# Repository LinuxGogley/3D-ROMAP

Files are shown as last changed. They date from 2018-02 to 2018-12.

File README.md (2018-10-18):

# CECS 490 - Senior Design Project
3D Robotic Mapping Platform (3D ROMAP) - designed at California State University Long Beach.

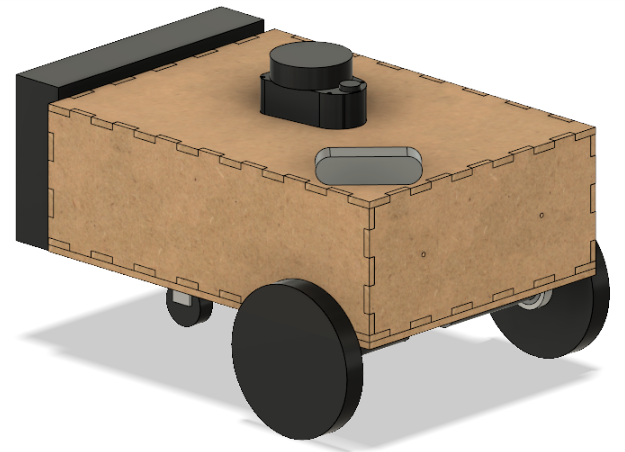
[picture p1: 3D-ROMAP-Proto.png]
Prototype Assembly


## Sponsored by Advanced Circuits
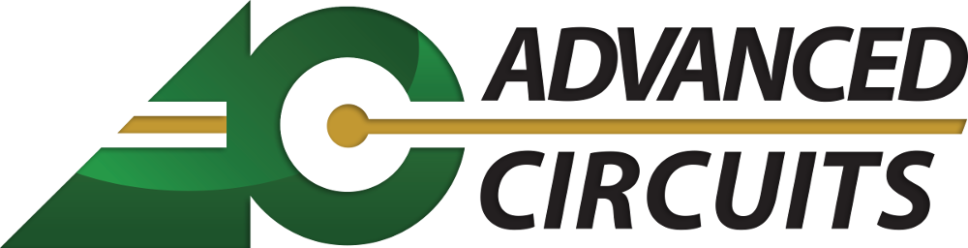
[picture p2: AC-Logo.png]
Sponsored By Advanced Circuits


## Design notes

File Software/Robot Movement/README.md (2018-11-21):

# Source code for Bluetooth Controlled Robotic Movement
* Uses bluetooth for wireless control of motors (WASD controls) 
* Uses two motors with seperate speed and direction controls
* Hardware: 
1. HC05 Bluetooth Module
2. MC33926 H-Bridge
3. TM4C Microcontroller
4. 2x DF Robot Motor 12V, 3.6A, 146RPM

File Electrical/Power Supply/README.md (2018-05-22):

# Power Supply
Schematic in PDF format, with directories containing source files and documentation pertaining to the power supply.

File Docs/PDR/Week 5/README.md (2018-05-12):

# PDR - 2018 April 22
PDR documents IMU, change from MS Kinect to Realsense, updated block diagram, and power
reqs updated.

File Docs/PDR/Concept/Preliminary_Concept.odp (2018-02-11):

## Preliminary Concept

TeaM4C (R Dominick, L Gogley, M Munoz, D Tran)

## Requirements

- The design shall map unknown coordinates through exploration.
  - Location of choice should not dictate mapping method, i.e. a room vs a field.
- The design shall not be limited to enclosed or man-made structures.
  - The scans must be accurate enough to recognize a low profile object as an obstacle/structure in its map.
- The design shall be capable of 2D SLAM.
  - SLAM shall be used to handle 2D mapping.
- The design shall be capable of 3D capture.
  - 3D capture can be pulled from samples or from real-time/soft real-time capture.
- The design shall be powered from an independent power supply.
  - This power source shall provide enough power to explore, at minimum, one floor of the ECS building.

## Limitations

- The design is not confined to color recognition of the surroundings.
  - With use of LiDAR, the capture is not interested in color, therefore detail is lost of surroundings.
- The design is not confined to autonomous navigation, simply the capability of such.
  - The design will be capable of mapping and localization, but the platform may not drive autonomously as functionality of mapping is the first priority.
- The design is not confined to real-time 3D mapping, due to limitations of price and available algorithms.
  - Real-time 3D is sometimes limited to ability of hardware readout, and may be an unrealistic endeavor. 3D may instead be done from sampling.
- The design is not interested in object recognition.
  - Point clouds will be used to simply display raw data, and points on a 2D plane will only be used to determine the explored area.

## Purpose of Design

- For us:
- Explore high performance embedded system design.
- Expand territory into industry applications such as point cloud capture, machine vision, and SLAM.

## Purpose of Design

- For the consumer:
- 3D maps introduce depth to a panoramic capture, and allow for implementations such as virtual real estate, virtual visits to landmarks, and cave, ocean, or other exploration.
- This platform will serve as a self-contained system capable of remembering where it began its journey, while also creating a map of the area it explores beyond that point.

## Top Level Block Diagram

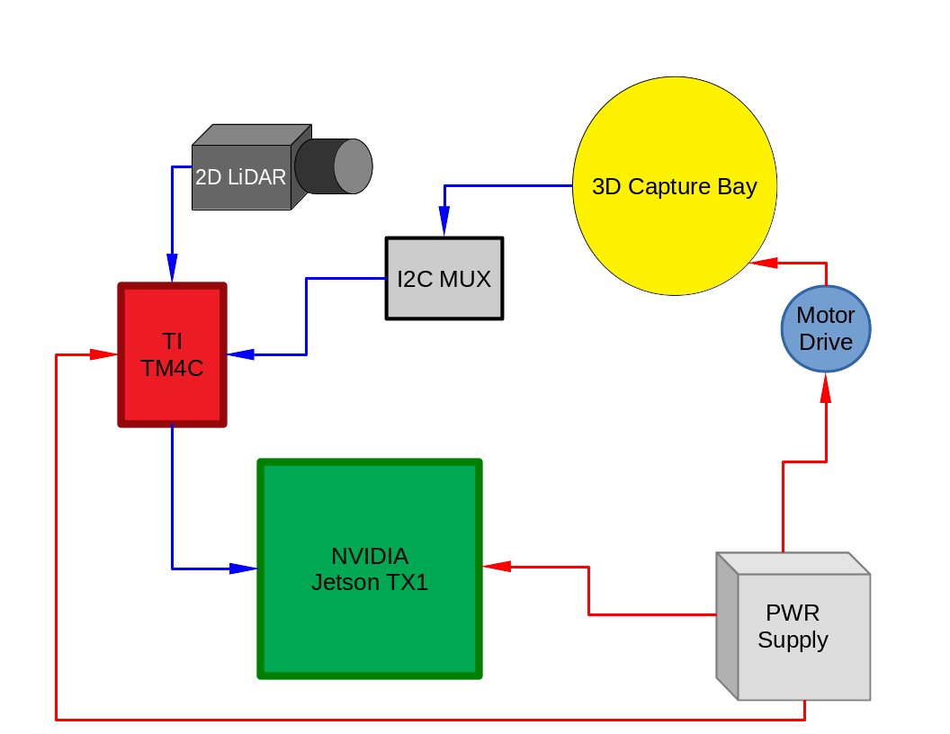
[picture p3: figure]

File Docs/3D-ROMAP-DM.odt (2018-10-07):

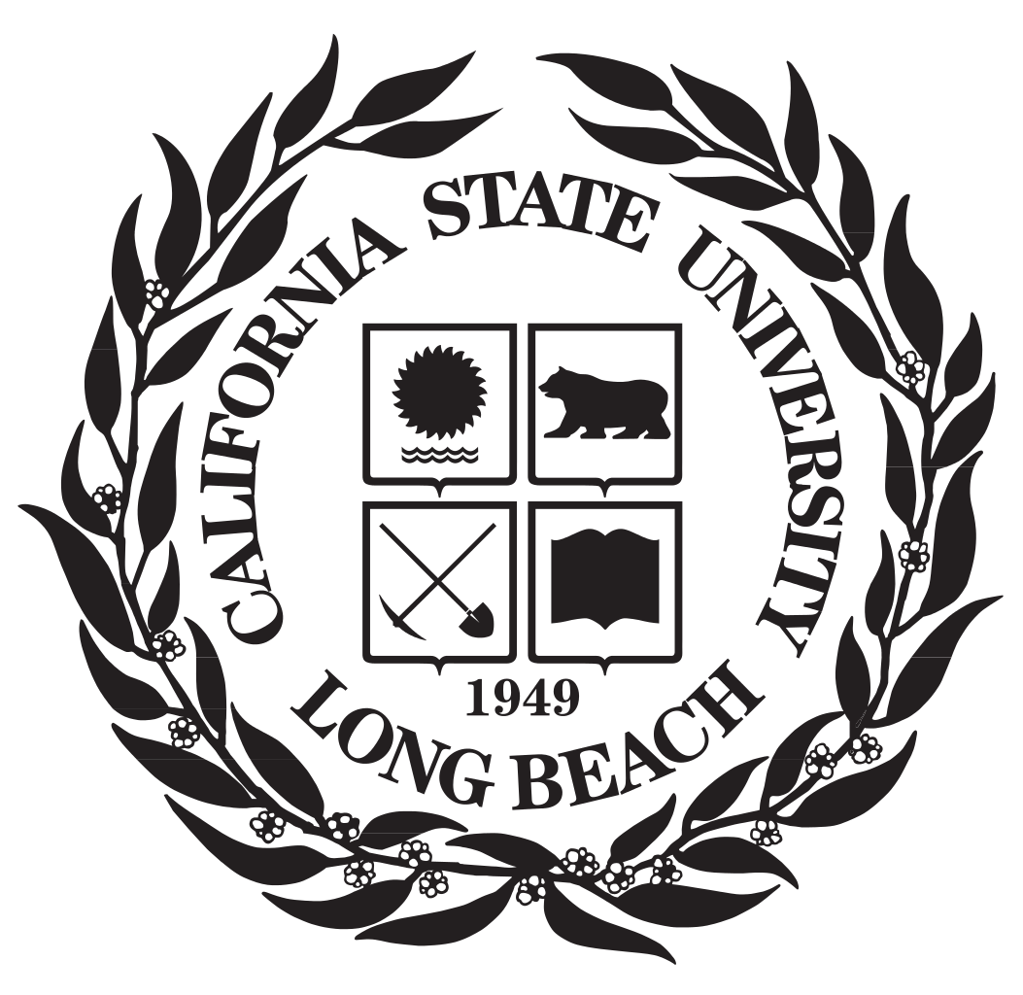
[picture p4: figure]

3D-ROMAP

Design & Methodology Document

CECS 490

Revision: C

California State University, Long Beach

The contents of this document may not be reproduced in whole or in part without the written

consent of the owner.

NOTICE

ALL STATEMENTS, INFORMATION, AND RECOMMENDATIONS IN THIS MANUAL ARE BELIEVED TO BE ACCURATE BUT ARE

PRESENTED WITHOUT WARRANTY OF ANY KIND. NOT WITHSTANDING ANY OTHER WARRANTY HEREIN, ALL DOCUMENT FILES

AND SOFTWARE ARE PROVIDED “AS IS” WITH ALL FAULTS. I DISCLAIM ALL WARRANTIES, EXPRESSED OR IMPLIED,

INCLUDING, WITHOUT LIMITATION, THOSE OF MERCHANTABILITY, FITNESS FOR A PARTICULAR PURPOSE AND

NON INFRINGEMENT OR ARISING FROM A COURSE OF DEALING, USAGE, OR TRADE PRACTICE.

IN NO EVENT SHALL I BE LIABLE FOR ANY INDIRECT, SPECIAL, CONSEQUENTIAL, OR INCIDENTAL DAMAGES, INCLUDING,

WITHOUT LIMITATION, LOST PROFITS OR LOSS OR DAMAGE TO DATA ARISING OUT OF THE USE OR INABILITY TO USE THIS

MANUAL, EVEN IF I HAVE BEEN ADVISED OF THE POSSIBILITY OF SUCH DAMAGES.

Rev History

Revision Number | Release Date | Description
A | 2018-03-22 | Initial release
B | 2018-05-22 | Preliminary data added
C

Index of Tables

Table of Figures

Preliminary Chassis Concept 16

Top Level Block Diagram 17

MCU detailed block diagram 18

Processing board detailed block diagram 23

Voltage rails and current 26

Power requirement and power draw per channel 26

Alkaline battery discharge 27

Deep cycle sealed lead acid discharge 28

LiFePO4 runtime discharge 28

LiFePO4 capacity discharge 29

18V and 12V DC-DC Converter 30

5V LDO to MCU and LiDAR 30

SLAM Software Flow 31

# Acronyms and Abbreviations

Abbreviation | Description | Abbreviation | Description
°C | Celsius | PCL | Point Cloud Library
°F | Fahrenheit | PWM | Pulse Width Modulation
A | Amps | Rev | Revision
COMM | Communication | SLAM | Simultaneous Localization and Mapping
CPU | Central Processing Unit | TBD | To Be Determined
dB | Decibels | UART | Universal Asynchronous Receiver Transmitter
ESD | Electrostatic Discharge | USB | Universal Serial Bus
FAT | File Allocation Table
FOV | Field of View
ft | Feet
g | Gram
GPU | Graphics Processing Unit
GUI | Graphical User Interface
mA | Milliamps
I²C | Inter-Integrated Circuit
I/O | Input/Output
ICD | Interface Control Document
ID | Identification
IR | Infrared
km | Kilometer
LDO | Low Dropout
LSB | Least Significant Bit
mm | Millimeter
ms | Millisecond
MSB | Most Significant Bit
NIR | Near Infrared
OEM | Original Equipment Manufacturer
PCD | Point Cloud Data

# Reference Documentation

The following documents form part of this specification. In the event of a conflict between

documents referenced herein and the contents of this specification, the contents of this specification

shall be considered a superseding requirement.

Document No:

# Scope

This document describes the design characteristics for the 3D-Robotic Mapping Platform (3D -ROMAP).

# Project Overview

The following research project documented in this report details a three-dimensional room mapping robot. The robot will be able to enter various rooms and be remotely controlled by the user. While the robot is in the specified environment, it will map the surrounding area in both a two-dimensional and three-dimensional representation. The user will then be able to view the generated maps on a separate remote desktop for observation purposes. The robot will combines various sensors in order to scan the environment around it and will utilize that data to determine its location in the current environment that it is exploring. This research project explores advanced image capturing techniques, navigation of unknown environments, as well as practical applications of electrical and mechanical engineering practices.

# Project Description

The implementation of our project involves the utilization of an onboard GPU-accelerated embedded computer that will process the data received from both the LiDAR sensor and the Intel Realsense IR Depth Camera. A cost-efficient microcontroller will also be utilized to interface with not only the LiDAR sensor but also the various motors including DC motors and a single stepper motor.

The LiDAR sensor will be mounted on platform that will be rotating at a fixed frequency through the use of a stepper motor. The LiDAR will return a distance value which will be utilized to generate a 2D representation of the environment. In order to accomplish this, the TM4C will send the both the distance value as well as the angle that the stepper motor is at to the Jetson board for processing. The Jetson will then generate a two-dimensional cartesian coordinate plane with those sampled points plotted on it, which will become the two-dimensional representation of the overall environment around the robot. The sensor along with the rotating platform will be mounted at the top of the robot’s chassis.

The Intel Realsense camera will be mounted at the front of the robot and will be utilized to extract depth and image data of the surrounding environment in front of it. The robot will capture the data at a fixed rate. This data will be output as a .pcd file format The data must then be filtered in order to reduce the distortion that occurs in the RGB point cloud capture for the user’s observability. After the data has been captured as a point cloud, the data will then be stitched with other point cloud captures in post-processing. Due to uncertainty with the data compilation not being able to keep up with real time capture rates, we will not be performing the stitching in real-time. Instead we will stitch the point clouds generated using an open source utility software called Cloud Compare.

The position of the robot in the given environment will be determined through the utilization of SLAM, or simultaneous localization and mapping. The details of the algorithm itself will be elaborated in a further section of this documentation.

These technologies will be powered from a custom-built power supply designed by us. We chose the NVIDIA Jetson TX1 to perform the main computations and instruction executions for various reasons including: its powerful processing capabilities, 256 CUDA core GPU, and the ability to load a flavor of Linux to debug and control the software running. Most of our focus will be distributed towards capturing and processing the data from the sensors, and point cloud generation of our given position in the environment. The 3D representation will be sent using a mounted commercial off the shelf (COTS) router to generate a local WiFi connection for remote desktop connection. A static IP will be assigned to the Jetson, and the remote protocols of interest are VNC, SSH, X2Go, and RDP.

# Similar Projects

MIT NVIDIA Jetson RACECAR:

Students at MIT developed a “Rapid Autonomous Complex-Environment Competing Ackermann-steering Robot”, or RACECAR using the NVIDIA Jetson TX1 to process the data from their sensory suite. The goal was to design and implement various SLAM algorithms that would allow the vehicle to navigate a tunnel fully autonomously without human intervention. Our project will also utilize the NVIDIA Jetson TX1 to process our sensory data and generate the 2D and 3D maps for the user to observe on a remote desktop. This project shows that the hardware has the power and capability to successfully perform the task.

DARPA SLAM Car:

In 2005, DARPA issued the DARPA Grand Challenge, which was a competition where driverless cars would compete on an off-road course to determine which vehicle could autonomously navigate it the fastest. The winning vehicle, named “Stanley”, successfully navigated the course the fastest with a time of 6 hours and 54 minutes. The vehicle utilized several technologies including: five LiDAR sensors to generate a 3D map of the environment to aid their GPS’s positional sensing capabilities, a video camera to observe driving conditions, and an odometer to calculate how far the vehicle had traveled if the other sensors could not extrapolate enough data to determine its given position. Six low-power computers running Linux operating systems were also used to process the sensor data. Our project will share a few similarities with this design, including the utilization of Linux OS on the NVIDIA Jetson TX1 to process and execute instructions based on the data obtained from our single LIDAR sensor. We will also be utilizing the LIDAR sensor to generate a 2D map rather than a 3D map; instead, we will use an Xbox Kinect to perform the 3D mapping of the environment.

# Project Significance

For our group, this project will serve as an in-depth introduction to vision systems, high performance embedded computing, power management, and exploration of robot localization techniques. This is intended as a research project in which the concepts listed above are implemented into a single functional design. We would hope that with further implementation, this research would result in possible consumer products such as advanced visual street maps and rescue platforms for victims of natural disasters.

# Requirements

In order to create a clear end goal for our design, the following requirements describe the necessary elements to satisfy our project of creating a 3D robotic mapping platform:

The design shall map unknown coordinates through exploration on passable terrain

The initial goal of the design was to be able to map an unknown location. The current build of the project is intended to be demonstrated in an office environment, so the qualification of “passable terrain” has been defined as our exploration environment.

The design shall be capable of 2D SLAM

To keep us directed towards the SLAM based side of the research, we have specified that the research should be capable of 2D SLAM with the implementation of the PulsedLight LiDAR Lite. 3D SLAM has been omitted as a requirement to ease completion.

The design shall be capable of 3D capture

Our design needs to be able to capture an environment in 3D in a point cloud format. Our capture must be real time, however the design does not have to process and stitch images together in real time. This condition has been limited to post processing, as we fear data compilation may not be able to keep up with real time capture rates.

The design shall be capable of producing a visual map from 3D capture

Individual 3D point clouds are required to be stitched together to form a completed 3D representation of the environment. Stitching two images together has prove to be successful manually, however the automation of this process is the end goal.

The design shall be powered from an independent power supply

A custom power supply is being designed for this project. While the battery source has yet to be selected, we are expecting a 24V input battery source. The power supply will efficiently step down the voltage to 18V and 12V using a DC-DC buck converter, and 5V using a 12V source through an LDO. The component of interest is the Texas Instruments TPS54531 for high current applications to the 18V and 12V rails, while the ST LD29150 will provide an efficient low power feed to the 5V rail to the MCU. During operation, the project should be capable of running a minimum of 20 min, which in turn allows for a 20 min room capture.

# Work Breakdown

Due to the complexity of this endeavour, we wanted to make efficient use of our large group by dividing the work into two teams of two. This ensures that both teams have at least one person to collaborate with, and that no members are excluded from meaningful contribution to the project.

The two teams will be assigned one categorical task which will encompass the heart of our design. These categories are: 3D capture and SLAM implementation.

These tasks will be our first priorities for our path to success, as they will create the baseline for our first working prototype. Below lists the two categories, and the requirements for fulfilling the task.

## 3D Capture

Intel Realsense Capture

Task to interface with the Intel Realsense D435 stereo vision camera using the official SDK. From this capture we will extract depth and image data from the surroundings to form matrices. Due to the inaccuracies of stereo vision technology, we will be sampling and filtering the data before generating a point cloud of the capture.

3D Point Cloud

Task to associate the IR distance data to image data in a rendered point cloud using the Realsense SDK, and the Point Cloud Library (PCL) platform to generate the 3 dimensional depth structures.

3D Rendering

Task to use 3D rendering software to generate the visual of our stitched result. This task will be accomplished by capturing the point cloud in a supported 3D format such as the Polygon (PLY) format or Point Cloud Data (PCD) format. The post-processing is accomplished with the Open-Sourced utility Cloud Compare, for the point cloud registration and stitching.

## Simultaneous Localization and Mapping (SLAM)

Algorithm

Task to research algorithms to track robot’s position as it explores a room. Our preliminary algorithm can be seen in flowchart format in the software section. The algorithm flows as follows: gather positional changes from movement sensors like the odometers and accelerometers, and use this data to create an initial estimate of where the robot is in its environment. Next, gather data from environmental sensors, such as the LiDAR distance sensor, relate it to data previously collected from the environmental sensors, and combine them to create a more accurate position estimation.

Hardware Capture

Task to research and prototype methods of capturing distance data of the surroundings to be used by SLAM. This includes distance measurements from our LiDAR sensor, positional change from motor odometers, angular velocity from our gyroscope, directional acceleration from our accelerometer, or changes in magnetism (essentially a compass).

SLAM Implementation

Task to implement the chosen algorithms with hardware to feed positional data to 3D rendering for completion of 3D mapping robot. Our implementation will be based on Google Cartographer, which incorporates range data (LiDAR Lite V1), IMU data (MPU-9250), and odometry data (wheel encoders) to enable our robot to simultaneously localize and map the environment around it in a two-dimensional implementation. We chose to utilize Google Cartographer because it is open source software and fits well with our selected components.

# Design Overview & Operation

Our robot design utilizes a microcontroller and an onboard processing computer to handle the various sub-components of the overall system. The microcontroller will handle motor control and will interface with an HC-05 bluetooth module as well as a LiDAR sensor. The onboard computer; the NVIDIA Jetson TX1, will be utilized to interface with our Intel Realsense IR stereo vision camera and will process and generate the 2D and 3D maps for our graphical user interface. The documentation below details each subcomponent in the design and its purpose within the overall system.

## NVIDIA Jetson TX1

An embedded development platform that has the capability of delivering quick processing of complex data as well as delivering the power efficiency needed for visual computing applications. It contains an onboard GPU that contains 256 CUDA cores that is needed to generate the point clouds effectively. This will be used as our main computing module which will process the data obtained from both the LIDAR sensor and the Xbox Kinect to generate both a 2D and 3D map of the environment around the robot. It will also be used to interface directly with the Intel Realsense camera itself to capture the point cloud data and process it. A Linux Operating System will also be loaded onto the platform to provide a suite for debugging the system with ease. The Jetson will also enable the ability for the design to remotely connect with a desktop to view the 2D map as well as the robot’s position within that given environment.

## Texas Instruments Tiva C Microcontroller

An embedded microcontroller that contains an I2C communication protocol necessary to interface with the LiDAR Lite sensor as well as hardware pulse-width modulation to control the DC motors. The TM4C was selected mainly due to the familiarity with the development board. The onboard debugging capability will also help with the development process by reducing the amount of time debugging the system. The TM4C will also relay the data captured from the LiDAR sensor to the Jetson board to decrease the computing load on the microcontroller itself. The TM4C will also be utilized to interface with the HC-05 bluetooth module to capture character inputs that will be processed by the TM4C and control the robot’s directional steering.

## HC-05 Bluetooth Module

The HC-05 bluetooth module will be utilized to capture data from a bluetooth terminal and transmit it over UART to the TM4C microcontroller. The captured character inputs will be utilized to allow the user to steer and control the direction that the robot navigates in the environment through the use of either an application on a smartphone or a physical controller.

## SLAMTED RP-LIDAR A1

The RP-LIDAR A1 sensor is a LIDAR sensor kit with a pre-configured DC motor belt drive and integrated microcontroller unit. The device captures distance readings and displays them on 2D Cartesian coordinates using the UART protocol, with a baud rate of 115200 and 8N1 stop bit configuration. The sensor has a max range of 12 meters, and a 8KHz sampling rate rotating at 5Hz. The data will be captured by spinning the unit continuously, and will be interpreted by a SLAM algorithm in order to pinpoint the robot’s position in the environment. This sensor was chosen due to its relatively lower cost in comparison to other LiDAR sensors combined with its ease of configuration and high speed data capture.

### LiDAR Verification

In order to verify that our LiDAR sensor functions correctly, we utilized an Arduino alongside with the prepackaged software that the manufacturers of the sensor provided for us. The software involved using the I2C communication protocol to capture the data readings from the lidar sensor. The data is returned as a split between the 8 upper bits as well as the 8 lower bits of data and are stored in an array. The contents of the array are then combined and shifted to generate the correct distance value as an integer. The distance is then displayed using the serial terminal on the Arduino IDE. We utilized the demo code and verified that the physical lidar sensor itself functions properly by observing the distance readings that are read through the I2C. We then studied the algorithm and ported the software over using the C language to the TM4C microcontroller. We then utilized an open source library that featured several pre-built functions that allowed us to use the I2C protocol on the TM4C to communicate with the lidar sensor. We declared the TM4C as the master and the sensor as the slave and began reading data from it. Rather than storing the upper and lower bits of data and combining them, we read a different address on the sensor that would return the both the upper and lower bits at once and saved it in a single variable. That variable was then displayed through a UART onto our serial terminal and we compared the distance values that were being captured with the Arduino code’s version. Both values were within range of one another, verifying that our port to the TM4C was a success and that the lidar sensor functions correctly.

## DC Motor H-Bridge

The L298N is an H-bridge that will be used to control our DC motors that will provide the robot with movement. This part was also chosen due to its relatively low cost and simplicity in interfacing with the TM4C microcontroller. Because of its low cost, this part acts as a test component before we move into a higher current rated H-Bridge for final implementation of the robot.

## MPU-9250 IMU

The MPU-9250 is an inertial measurement unit that contains 9 degrees of freedom, or 9-axis motion processing. It contains an accelerometer for measuring x,y, and z directional acceleration, a gyroscope for measuring x,y, and z angular velocity, and a magnetometer which is essentially a compass. The MPU-9250 will be utilized in the design to assist in the SLAM algorithm for tracking the robot’s position in the environment. Currently testing to see whether we can extract positional data from our visual maps to determine the necessity of utilizing this sensor in the design.

## Intel Realsense Depth Camera

The Intel Realsense is an structured-light, active infrared stereo vision depth camera that will utilized to capture 3D point cloud data rather than the Xbox Kinect in our future iterations. The sensor allows for image overlay as well as the utilization of point clouds for depth representation. We chose to switch to this specific sensor due to the sensor’s well-documented development platform: the Realsense SDK. It is a library that allows us to utilize the sensor and capture point cloud data and export it as data to file. It also provides a relatively extensive debugging environment that generates camera log files, frame statistic reports, and firmware test commands that can be sent directly to the camera itself. The camera also allows us to associate RGB values with specific points on the cloud rather than having us overlay the RGB values post-processing. The Realsense camera also has wider viewing angles in comparison to the Kinect which allows for a faster rate of data capture. The RGB camera and IR camera have an FOV of 69.4° and 85.2° respectively.

## Preliminary Chassis

The chassis is constructed from aluminum extrusion. Extrusions are held together via angle brackets and t-slot nuts and an assortment of m3 and m4 sized fittings. Faces of the rover’s body are constructed of MDF. All major components are mounted to the chassis with fasteners and 3D printed parts. Expected volume of the rover is estimated to be somewhere around 300x300x300mm. However not all hardware components have been finalized and this may be adjusted in the future.

The following figure details a prototype of the robot chassis:

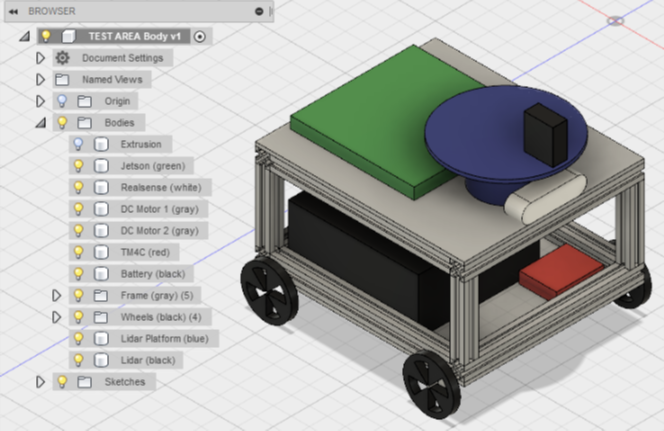
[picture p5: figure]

Illustration 1: Preliminary Chassis Concept

# Preliminary Block Diagram

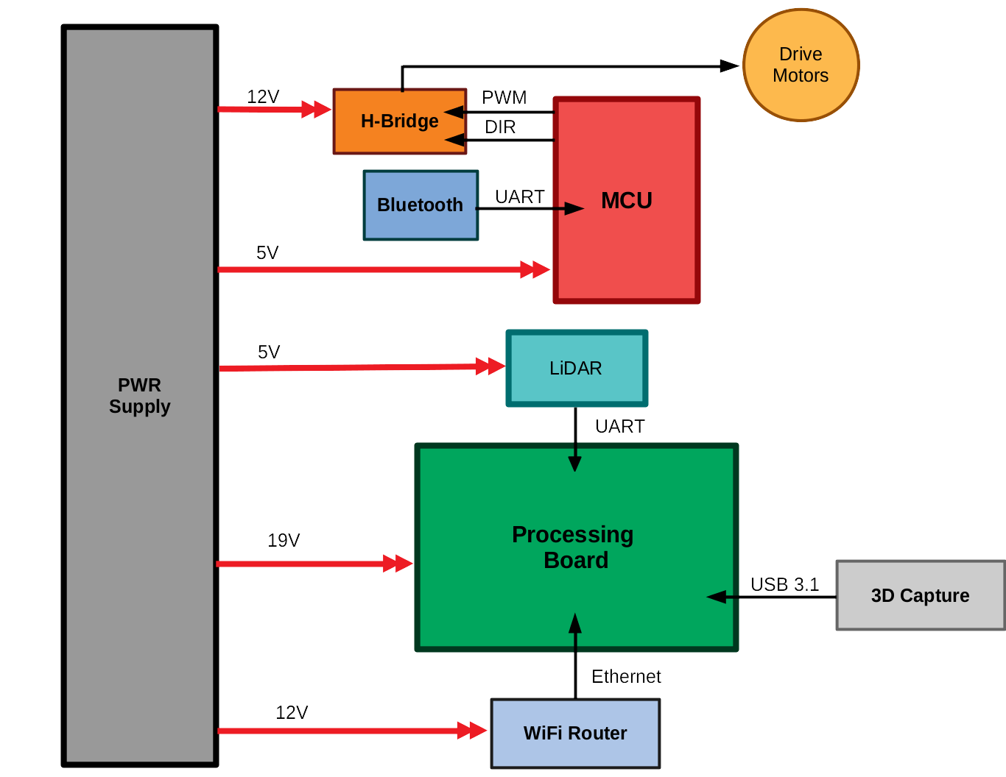
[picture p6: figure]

Illustration 2: Top Level Block Diagram

The preliminary Block Diagram shows a top level view of parts used in the design as well as the power and data rails interconnecting each. The power supply is currently estimated to be a 24V source that will be stepped down to 18V, 12V, and 5V for the respective components. Red arrows denote power delivery to the electronics, and black arrows denote communication signals and their direction. The bold yellow arrow denotes communication from the LiDAR to the MCU and finally to the Processing board.

# Detailed Block Diagrams

## Microcontroller Detailed Block Diagram

The following functional block diagram details the port connections and signals for the TM4C microcontroller portion of the robot design. The diagram also details all ports that will be utilized on the microcontroller itself for various alternative functionalities including UARTs, I2C, and PWM generators.

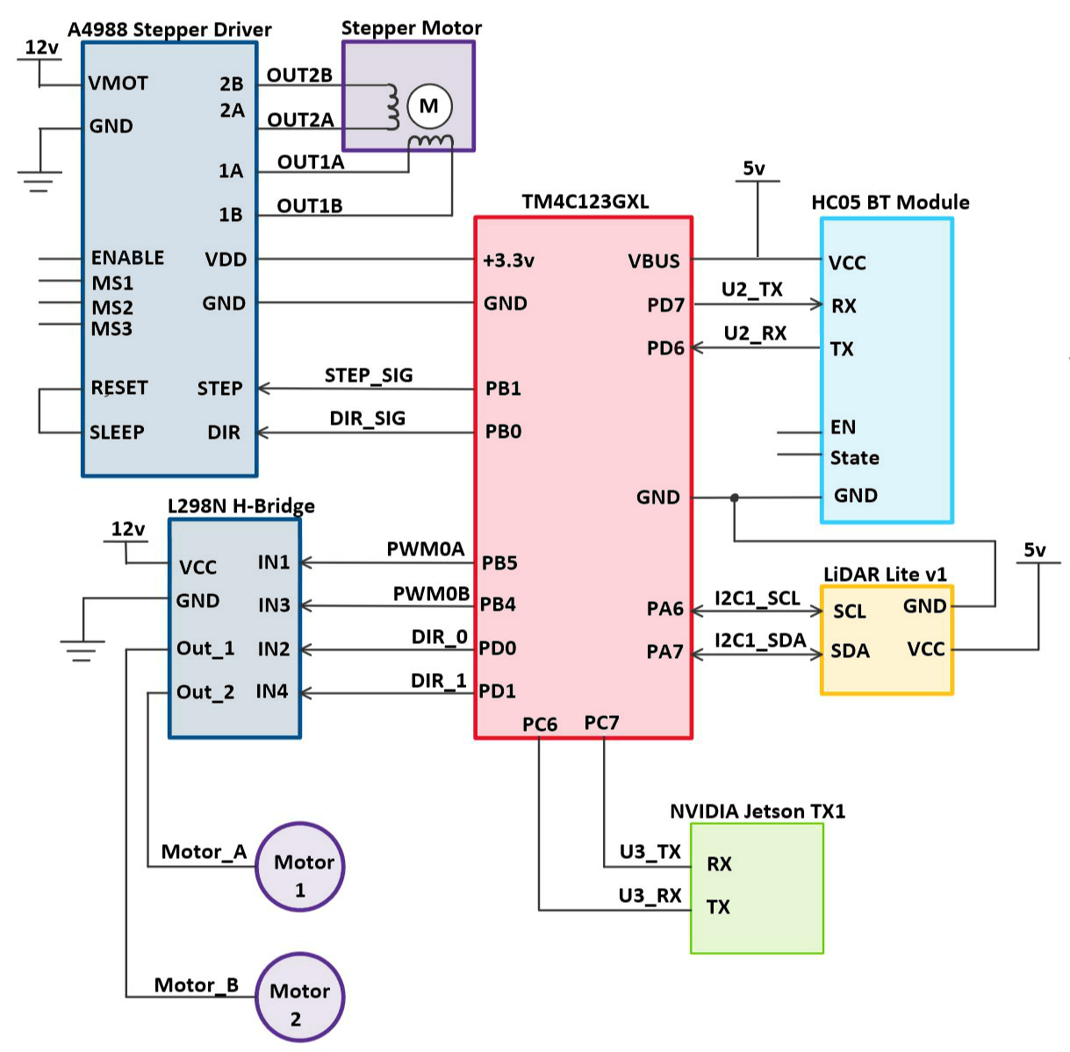
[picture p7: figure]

Illustration 3: MCU detailed block diagram

The following charts will detail various aspects of each module including the signal names, descriptions, signal types, voltage and current requirements, and their operation.

TM4C123GXL Description Table

Signal Name | Signal Description | Signal Type | Voltage Level | Current Req. | Operation
+3.3v | Regulated 3.3v from microcontroller | Power Output | 3.3v | 300mA (Max) | Provides an output of 3.3v to the A4988 stepper motor driver
VBUS | Input to power the microcontroller and output regulated 5v from microcontroller | Power Input/ Output | 5v (+/-0.25v) | 323mA (Max) | 5v input to power the entire microcontroller and outputs 5v to power the HC05 bluetooth module
PWM0A (PB5) | PWM signal output | Digital Output | 0v to 3.3v | N/A | Provides a pulse-width modulated signal to the L298N H-Bridge to control the speed of rotation on DC motors
PWM0B (PB4) | PWM signal output | Digital Output | 0v to 3.3v | N/A | Provides a pulse-width modulated signal to the L298N H-Bridge to control the speed of rotation on DC motors
DIR_0 (PD0) | GPIO Output | Digital Output | 0v to 3.3v | N/A | Provides an output signal to the L298N H-Bridge to control the directional rotation of the DC Motors
DIR_1 (PD1) | GPIO Output | Digital Output | 0v to 3.3v | N/A | Provides an output signal to the L298N H-Bridge to control the directional rotation of the DC Motors
U2_TX (PD7) | UART Functionality (TX) | Digital Output | 0v to 3.3v | N/A | Transmits characters to the HC05 for configuration purposes
U2_RX (PD6) | UART Functionality (RX) | Digital Input | 0v to 3.3v | N/A | Receives characters from the HC05 for steering control
U3_TX (PC7) | UART Functionality (TX) | Digital Output | 0v to 3.3v | N/A | Transmits LiDAR distance data to the NVIDIA Jetson TX1 for processing
U3_RX (PC6) | UART Functionality (RX) | Digital Input | 0v to 3.3v | N/A | In case we need to relay data from the Jetson to the TM4C

HC05 Bluetooth Module Description Table

Signal Name | Signal Description | Signal Type | Voltage Level | Current Req. | Operation
VCC | Power input to utilize module | Power Input | 3.3v to 5v | 35mA | Power input of 3.3v to 5v to turn on module
RX | UART Functionality (RX) | Digital Input | 0v to 3.3v | 35mA | Data input through UART communication for module configuration
TX | UART Functionality (TX) | Digital Output | 0v to 3.3v | 35mA | Transmits data received from a bluetooth terminal to the TM4C
EN | Power enable to switch to configuration mode | Power Input | 3.3v | 35mA | Only connected when configuring settings for HC05 module; otherwise unconnected during operation
State | N/A | N/A | N/A | N/A | Unconnected

LiDAR Lite v1 Sensor Description Table

Signal Name | Signal Description | Signal Type | Voltage Level | Current Req. | Operation
VCC | Power input to utilize sensor | Power Input | 5v | 130mA Max | Power input to sensor
SCL | I2C Functionality (Clock Signal) | Digital Input | 0v to 3.3v | 130mA | Clock signal input for I2C communication between TM4C and LiDAR sensor
SDA | I2C Functionality (Data Line) | Digital Input/ Output | 0v to 3.3v | 130mA | Data line to communicate data between TM4C and LiDAR sensor

L298N H-Bridge Description Table

Signal Name | Signal Description | Signal Type | Voltage Level | Current Req. | Operation
VCC | Voltage input to power the DC Motors | Power Input | 12v | 2A | Power input of 12v to power both DC motors
PWM0A (IN1) | Logical Input to H-Bridge | Digital Input | 0v to 3.3v | N/A | PWM Signal to logical Input of H-Bridge to control DC Motor 1
PWM0B (IN3) | Logical Input to H-Bridge | Digital Input | 0v to 3.3v | N/A | PWM Signal to logical Input of H-Bridge to control DC Motor 2
DIR_0 (IN2) | Logical Input to H-Bridge | Digital Input | 0v to 3.3v | N/A | GPIO Output signal to logical Input of H-Bridge to control directional rotation of DC Motor 1
DIR_1 (IN4) | Logical Input to H-Bridge | Digital Input | 0v to 3.3v | N/A | GPIO Output signal to logical Input of H-Bridge to control directional rotation of DC Motor 2
Motor_A (Out_1) | Voltage Output to DC Motor | Power Output | 12v | 2A | Power Output to provide rotation for DC Motor 1
Motor_B (Out_2) | Voltage Output to DC Motor | Power Output | 12v | N/A | Power Output to provide rotation for DC Motor 2

A4988 Stepper Driver Description Table

Signal Name | Signal Description | Signal Type | Voltage Level | Current Req. | Operation
VMOT | Voltage input to power the stepper motor | Power Input | 12v | 4A max | Power input of 12v to power the stepper motor
VDD | Voltage input to power the stepper driver | Power Input | 3.3v | 8mA | Power input of 3.3v to power the stepper driver
STEP_SIG (STEP) | Step Input to Stepper Driver | Digital Input | 0v to 3.3v | N/A | GPIO Output signal from TM4C to control the steps of the motor
DIR_SIG (DIR) | Direction Input to Stepper Driver | Digital Input | 0v to 3.3v | N/A | GPIO Output signal from TM4C to control the direction the motor steps in
OUT2B (2B) | Stepper Output to coil of Stepper Motor | Power Output | 8v to 35v | N/A | Power Output signal from stepper to coil 1 of stepper to provide rotation
OUT2A (2A) | Stepper Output to coil of Stepper Motor | Power Output | 8v to 35v | N/A | Power Output signal from stepper to coil 1 of stepper to provide rotation
OUT1A (1A) | Stepper Output to coil of Stepper Motor | Power Output | 8v to 35v | N/A | Power Output signal from stepper to coil 2 of stepper to provide rotation
OUT1B (1B) | Stepper Output to coil of Stepper Motor | Power Output | 8v to 35v | N/A | Power Output signal from stepper to coil 2 of stepper to provide rotation

## Microcontroller Detailed Block Diagram

The following functional block diagram details the port connections and signals for the NVIDIA Jetson TX1 processing board portion of the robot design. The diagram details all modules that will be interfacing with the Jetson including the Intel Realsense camera for 3d capture, a router to provide a wifi connection to the Jetson, an IMU, and the TM4C to process the data coming from the microcontroller.

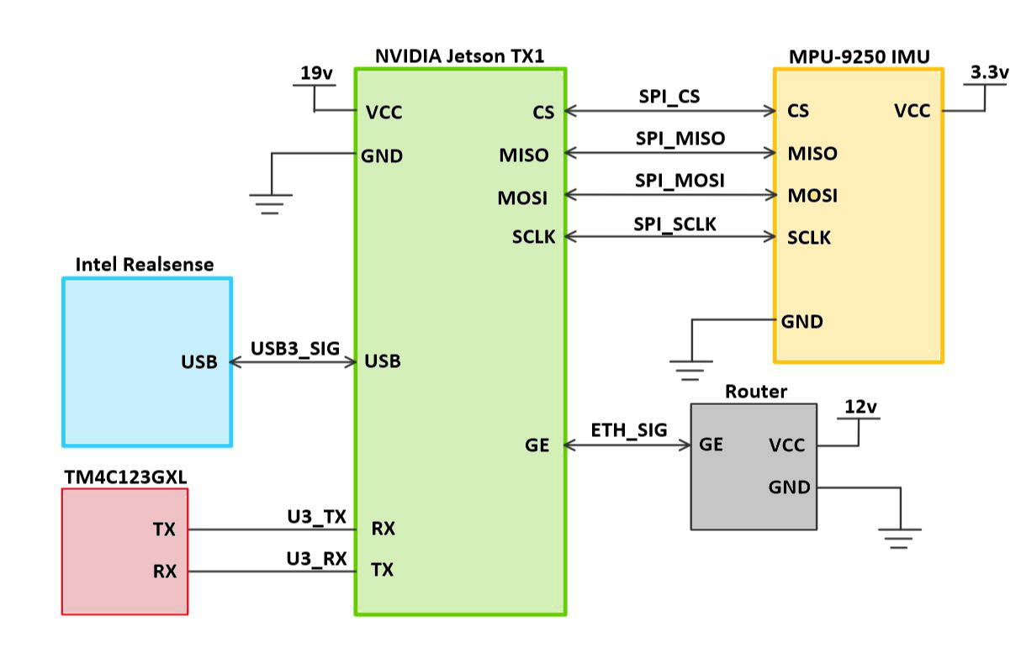
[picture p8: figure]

Illustration 4: Processing board detailed block diagram

The following charts will detail various aspects of each module including the signal names, descriptions, signal types, voltage and current requirements, and their operation.

NVIDIA Jetson TX1 Description Table

Signal Name | Signal Description | Signal Type | Voltage Level | Current Req. | Operation
VCC | Input to power the processing board | Power Input | 5v-19v | 0.8A | Power input to Jetson TX1
USB | USB 3.1 Port for data communication | Digital Input/ Output | 5v | N/A | USB communication to capture data from the Intel Realsense camera to the Jetson for processing
U3_TX (RX) | UART Functionality (RX) | Digital Output | 0v to 3.3v | N/A | Receives LiDAR distance data from the TM4C for processing
U3_RX (TX) | UART Functionality (TX) | Digital Input | 0v to 3.3v | N/A | In case we need to relay data from the Jetson to the TM4C
GE | Gigabit Ethernet Connection | Digital Input/ Output | N/A | N/A | Port connects to a router using an ethernet cable to provide a WIFI connection to the Jetson

MPU-9250 IMU Sensor Description Table

Signal Name | Signal Description | Signal Type | Voltage Level | Current Req. | Operation
VCC | Power input to utilize IMU sensor | Power Input | 3.3v | 8µA - 3.7mA | Power input of 3.3v to power on sensor. Current requirement dependent on number of axis utilized on IMU
CS | Chip Select for SPI utilization | Digital Input | 0v to 3.3v | N/A | Port to switch between I2C and SPI utilization on the IMU interface
SPI_MISO (MISO) | Master-In, Slave-Out signal for SPI communication | Digital Input/ Output | 0v to 3.3v | N/A | Port to read data from the IMU(Slave) to the Jetson(Master)
SPI_MOSI (MOSI) | Master-Out, Slave-In signal for SPI communication | Digital Input/ Output | 0v to 3.3v | N/A | Port to write data from the Jetson(Master) to the IMU(Slave)
SPI_SCLK (Clock Signal) | SPI Functionality (Clock Signal) | Digital Output | 0v to 3.3v | N/A | Port outputs a common clock signal between the Jetson and the IMU

Intel Realsense Depth Camera Description Table

Signal Name | Signal Description | Signal Type | Voltage Level | Current Req. | Operation
USB | USB3.1 Provides power and communication | Power & Data I/O | 5v | N/A | Power input and communication between the Jetson and the Realsense camera

Router Description Table

Signal Name | Signal Description | Signal Type | Voltage Level | Current Req. | Operation
VCC | Power input to utilize router | Power Input | 12v | 1.5A (Max) | Voltage input of 12v to power on the Router
GE | Gigabit Ethernet Connection | Data Input | N/A | N/A | WiFi connection to the Jetson for remote access

# Power Analysis

The robot is projected to house two separate battery sources for the motor drive and electronics power supply board to isolate motor noise. Below is a table of estimated voltage requirements, and the estimated current draw in amps. This is used to help select an appropriate voltage regulator per voltage supply. The second table notes the total power draw per voltage source to help determine the appropriate battery chemistry for our device.

Illustration 5: Voltage rails and current

From these results we determined a 24V power source was necessary to meet the 18V requirement for the Jetson, and analyzed our options for runtime and battery chemistry. In order to calculate our total runtime minimum to meet the 20 minute operating requirement, we used the following formula:

Runtime = (10 * Ampere Hours) / Load in Watts

Assuming a 7Ah (Amp hour) rated battery, at ideal conditions, our runtime would be:

Illustration 6: Power requirement and power draw per channel

0.57 Hours = (10 * 7Ah) / 122.1W

With this result we then evaluated the pros and cons of various battery sources. In order to achieve the power draw we necessary for our application, standard alkaline batteries would be a poor choice due to their inability to be recharged, poor discharge characteristics, low current delivery, and low voltage all leading to an unrealistic endeavour of inconsistent discharges, high quantities of batteries, and excessive waste.

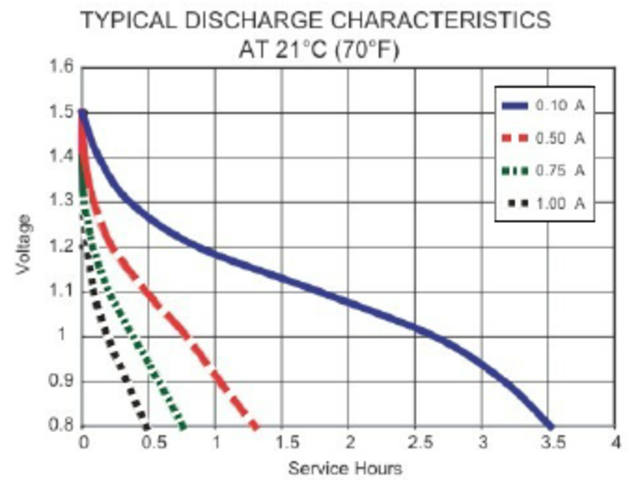
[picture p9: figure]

Illustration 7: Alkaline battery discharge

From this evaluation, we could also disregard the NiMH cells due to their low voltage characteristics, and the unreasonable quantity to achieve the energy density we need. In addition, we also chose to disregard Lithium Ion batteries from our selection due to their unsafe nature, lack of 24V sources at high amp hours, inability to safely connect two sources in series, and overall cost to achieve any reasonable results.

After we conducted our analysis of these options, we assumed sealed lead acid (SLA) batteries would yield the best results for our application due to their robust nature, price for performance, recharge capabilities, and endurance for more power aggressive applications.

However, after evaluating the various types of SLAs, we found that due to their weight, and 50% capacity discharge threshold, that the power source would be less than ideal to achieve our runtime. In order to be certain our robot would be capable of supplying the correct voltage rails without damaging our battery source, we would need to purchase batteries with a rating of 10Ah or more to achieve at least 24 minutes. For the price, if we further explore this technology we have explored the options of deep cycle SLA at a higher Amp-hour rating due to their better performance for our application of power usage. Below is the discharge curve for a deep cycle SLA from PowerSonic.

An additional chemistry we have explored is Lithium Iron Phosphate, due to their 70% discharge threshold, an average of 40% lighter than SLAs, and lowered volatile nature over Lithium Ion. The only reason we would not consider this as a solution to our robot, is the cost associated with the power source. At 7Ah we are looking at an average of $130 for a pair vs $30 for a standard SLA pair. Below are the discharge curves of both the SLA and the LiFePO4 batteries.

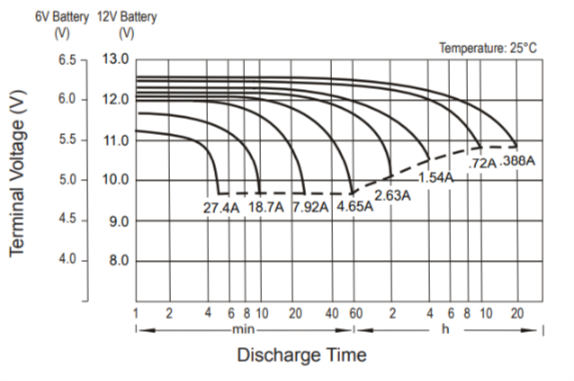
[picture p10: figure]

Illustration 8: Deep cycle sealed lead acid discharge

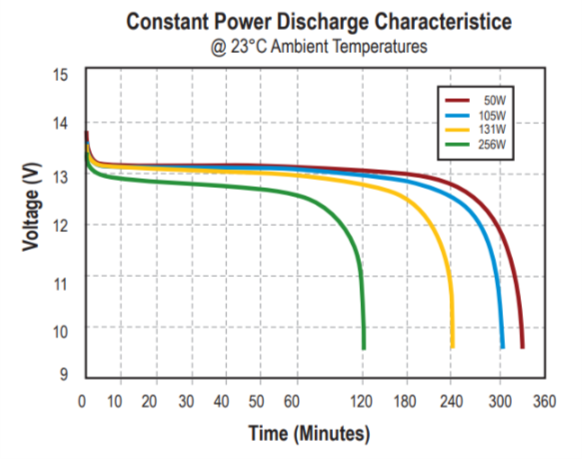
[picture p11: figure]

Illustration 9: LiFePO4 runtime discharge

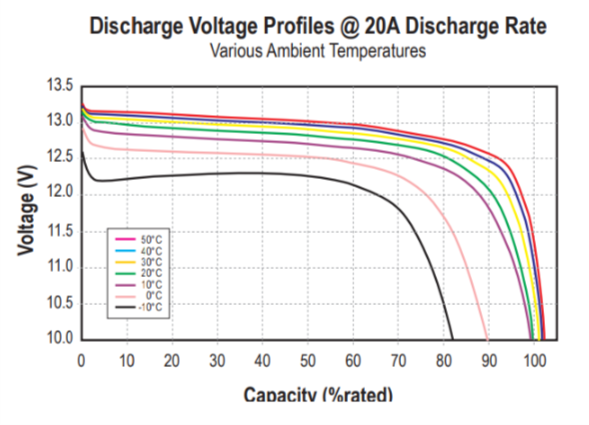
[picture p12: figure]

Illustration 10: LiFePO4 capacity discharge

# Hardware Design

## Texas Instruments - TPS54531

The TPS354531 is a high efficiency, high current DC-DC buck converter used to source the 18V and 12V electronics in our design. The max current allowed from this regulator is 5A, which is perfect for our 2A motors, and max current draw of 4A of our Jetson. This chip is also inexpensive for our design, and in a compact SMT package.

The formula used to calculate the minimum inductance for our requirements is as follows:

L rsub{min} = {V rsub{out} (Vin rsub{MAX} - V rsub{out} )} over {Vin rsub{MAX} * K rsub {IND} * I rsub{out} * f rsub{sw}}

From this equation we get 100uH minimum required inductance for a lightest load of 0.5A. To derive this value, we select a Vout of 12V and 18V, a Vin (max) of 24V, an Iout of 0.5A, a switching frequency of 570KHz, and a constant K of 0.2 for higher ESR coefficient.

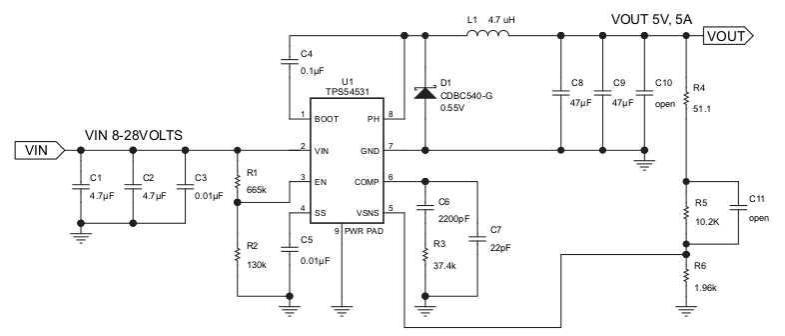
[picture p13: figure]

Illustration 11: 18V and 12V DC-DC Converter

To achieve the voltages desired we used the following formula:

R6`=`{10K (0.8V)} over {Vout - 0.8V}`=`{R5 (Vref)} over {Vout - Vref}

For 18V we achieved the R6 voltage divider value of 440, and for 12V we achieved the resistor value of 714. See schematic for circuit implementation.

## ST Micro - LD29150

The LD29150 very low dropout 5V LDO regulator is used to source 5V to our MCU and LiDAR from the 12V voltage of the router supply. The max current allowed from this regulator is 1.5A, and will both reduce ripple and reduce the inductance requirement on our DC-DC converter.

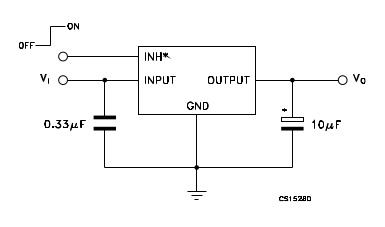
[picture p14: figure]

Illustration 12: 5V LDO to MCU and LiDAR

# Software Design

The following software flow chart details the overview that our SLAM algorithm will take to provide our system with an accurate estimate position of where it is in the room. During the LiDAR Reading stage, our Jetson will be reading the most recent samples from the LiDAR sensor, which will be send into the landmark extraction stage where the system will detect objects in the environment such as walls, chairs, furniture, etc. The Jetson will then compare the objects that are currently being detected and compare it to objects that have been detected in the past. During the re-observation and new observations stage, the algorithm will determine if a given object has been seen in the past. If the object has not been seen before, it will be marked as a new object and added to the list of recognized objects that are used in the data association step. However, if the object has been seen before, during the re-observation stage the Jetson will combine the distance data from the LiDAR and the current estimate position to create a new, more accurate estimated position. Lastly, as the wheels keep turning the odometry data is updated and the cycle repeats.

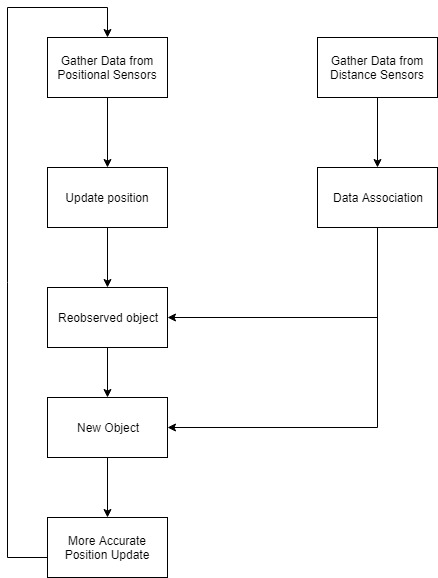
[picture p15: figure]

Illustration 13: SLAM Software Flow

The software that we plan to utilize for the environment mapping portion of the design involves capturing data for both the 2D and 3D map rendering. The 2D portion of the design involves interfacing with the LiDAR sensor through I2C, capturing the distance values it returns, and plotting it on a two-dimensional cartesian plane. In order to generate the plane, we must utilize both the distance the sensor detects as well as the angle that the sensor is facing. This angle is given by the stepper motor’s orientation. Every sampled point is then plotted on the plane, where eventually the plane itself becomes the 2D representation of the environment around it.

The 3D portion of the design involves programming the camera to capture a frame of data, or point cloud, and output the data as a file format at a fixed rate. The file format ideally should be a .pcd type format in order for us to utilize the point cloud library and stitch multiple clouds together. These stitches allow us to generate a 3d representation of the environment around the robot.

# Referenced External Documentation

[1]P. Henry, M. Krainin, E. Herbst, X. Ren and D. Fox, "RGB-D mapping: Using Kinect-style depth cameras for dense 3D modeling of indoor environments", The International Journal of Robotics Research, vol. 31, no. 5, pp. 647-663, 2012.

[2]K. Khoshelham and S. Elberink, "Accuracy and Resolution of Kinect Depth Data for Indoor Mapping Applications", Sensors, vol. 12, no. 2, pp. 1437-1454, 2012.

[3]N. Namitha, S. Vaitheeswaran, V. Jayasree and M. Bharat, "Point Cloud Mapping Measurements Using Kinect RGB-D Sensor and Kinect Fusion for Visual Odometry", Procedia Computer Science, vol. 89, pp. 209-212, 2016.

[4]P. Tarkowski, I. Malujda, K. Talaśka, M. Kukla and J. Górecki, "Adjustment of the Distance of Objects to the Microsoft Kinect Device Fitted with Nyko Zoom Attachment Used in a Three-axis Manipulator", Procedia Engineering, vol. 177, pp. 387-392, 2017.

[5]M. Chang and Z. Kang, "AN INDOOR SLAM METHOD BASED ON KINECT AND MULTI-FEATUREEXTENDED INFORMATION FILTER", ISPRS - International Archives of the Photogrammetry, Remote Sensing and Spatial Information Sciences, vol. -27, pp. 327-332, 2017.

[6]C. Bellés and F. Pla, "A Kinect-Based System for 3D Reconstruction of Sewer Manholes", Computer-Aided Civil and Infrastructure Engineering, vol. 30, no. 11, pp. 906-917, 2014.

[7]L. Lu, R. Tao and G. Jin, "A Low-Cost 3D Local Mapping and Localization Method", Applied Mechanics and Materials, vol. 556-562, pp. 4089-4092, 2014.

[8]L. Zhang, P. Shen, G. Zhu, W. Wei and H. Song, "A Fast Robot Identification and Mapping Algorithm Based on Kinect Sensor", Sensors, vol. 15, no. 8, pp. 19937-19967, 2015.

[9]K. Kamarudin, S. Mamduh, A. Shakaff and A. Zakaria, "Performance Analysis of the Microsoft Kinect Sensor for 2D Simultaneous Localization and Mapping (SLAM) Techniques", Sensors, vol. 14, no. 12, pp. 23365-23387, 2014.

[10]T. Taketomi, H. Uchiyama and S. Ikeda, "Visual SLAM algorithms: a survey from 2010 to 2016", IPSJ Transactions on Computer Vision and Applications, vol. 9, no. 1, 2017.

[11]"Documentation - Point Cloud Library (PCL)", Pointclouds.org, 2018. [Online]. Available: http://www.pointclouds.org/documentation/. [Accessed: 07- Apr- 2018].

[12]"OpenGL Programming - Wikibooks, open books for an open world", En.wikibooks.org, 2018. [Online]. Available: https://en.wikibooks.org/wiki/OpenGL_Programming. [Accessed: 07- Apr- 2018].

[13]Ocw.mit.edu, 2018. [Online]. Available: https://ocw.mit.edu/courses/aeronautics-and-astronautics/16-412j-cognitive-robotics-spring-2005/projects/1aslam_blas_repo.pdf. [Accessed: 07- Apr- 2018].

[14]"rgbdslam - ROS Wiki", Wiki.ros.org, 2018. [Online]. Available: http://wiki.ros.org/rgbdslam. [Accessed: 07- Apr- 2018].

[15]"Stanley (vehicle)", En.wikipedia.org, 2018. [Online]. Available: https://en.wikipedia.org/wiki/Stanley_(vehicle). [Accessed: 07- Apr- 2018].

[16]"OpenSLAM.org", Openslam.org, 2018. [Online]. Available: http://openslam.org/. [Accessed: 07- Apr- 2018].

3D-ROMAP Rev. C

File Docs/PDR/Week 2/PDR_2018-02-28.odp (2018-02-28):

## PDR Week 2

TeaM4C (R Dominick, L Gogley, M Munoz, D Tran)

## Requirements

- The design shall map unknown coordinates through exploration on passable terrain.
  - Location of choice should not dictate mapping method, i.e. a room vs a field.
- The design’s structural capture shall not be limited by low light settings.
  - The scans must be accurate enough to recognize a low profile object as an obstacle/structure in its map.
- The design shall be capable of 2D SLAM.
  - SLAM shall be used to handle 2D coordinate recognition, and assist in 3D sampling.
- The design shall be capable of 3D capture.
  - 3D capture can be pulled from samples or from real-time/soft real-time capture.
- The design shall be powered from an independent power supply.
  - This power source shall provide enough power to explore, at minimum, 20 minutes of capture.

## Limitations

- The design is not confined to low light, visible image capture.
  - High resolution 3D structural capture is used to compensate for loss of visuals under low light.
- The design is not confined to autonomous navigation, simply the capability of such.
  - The design will be capable of mapping and localization, but the platform may not drive autonomously as functionality of mapping is the first priority.
- The design is not confined to real-time 3D mapping, due to limitations of price and available algorithms.
  - Real-time 3D is sometimes limited to ability of hardware readout, and may be an unrealistic endeavor. 3D may instead be done from sampling.
- The design is not interested in object recognition.
  - Point clouds will be used to simply display raw data, and points on a 2D plane will only be used to determine the explored area.

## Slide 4

Systems Engineering

## Top Level Block Diagram

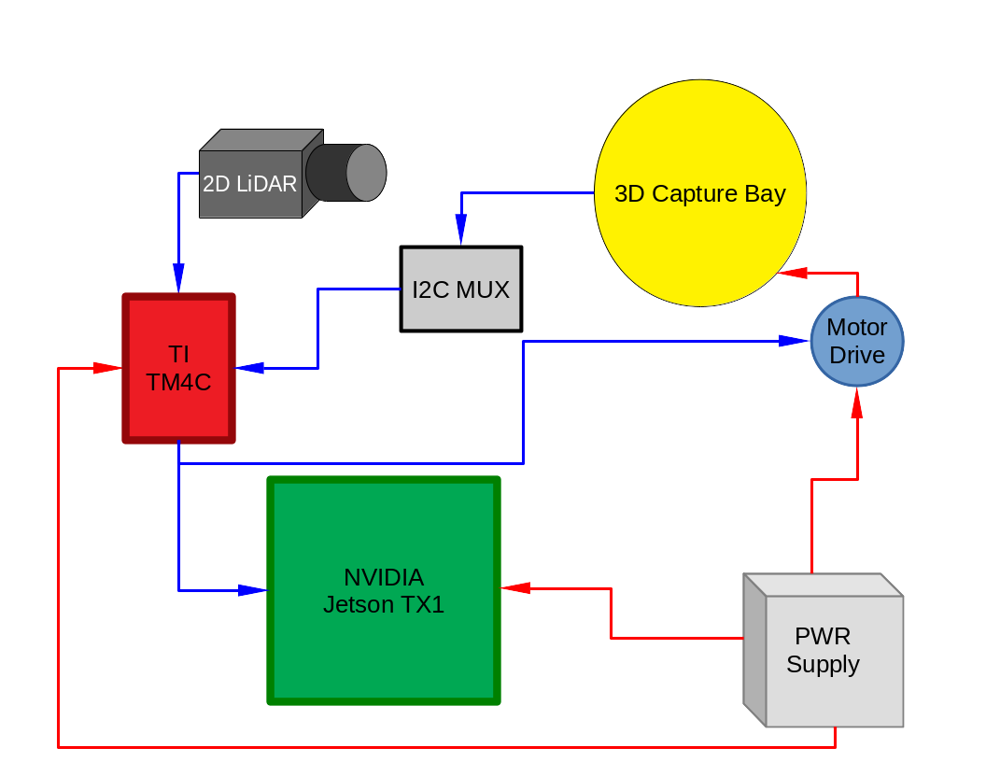
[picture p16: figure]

## 3D Capture

- LiDAR

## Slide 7

Mechanical Engineering

## Top Level Motor Assembly

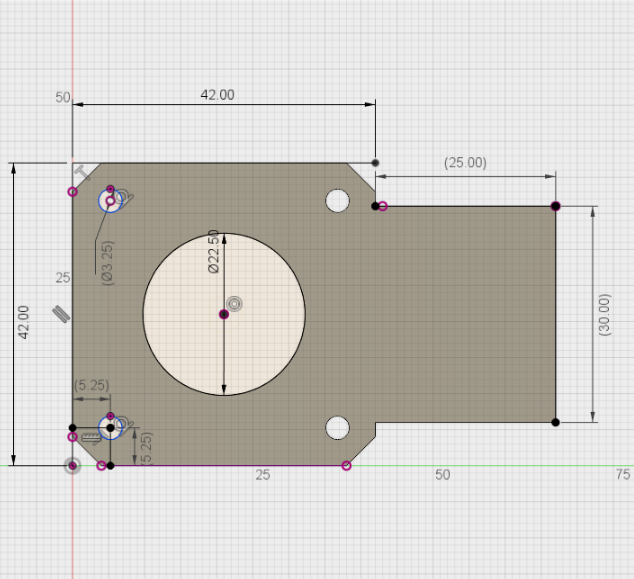
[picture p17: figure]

- 3D capture bay assembly, driven by stepper.

## Motor Mount Assembly

- Motor drive support assembly

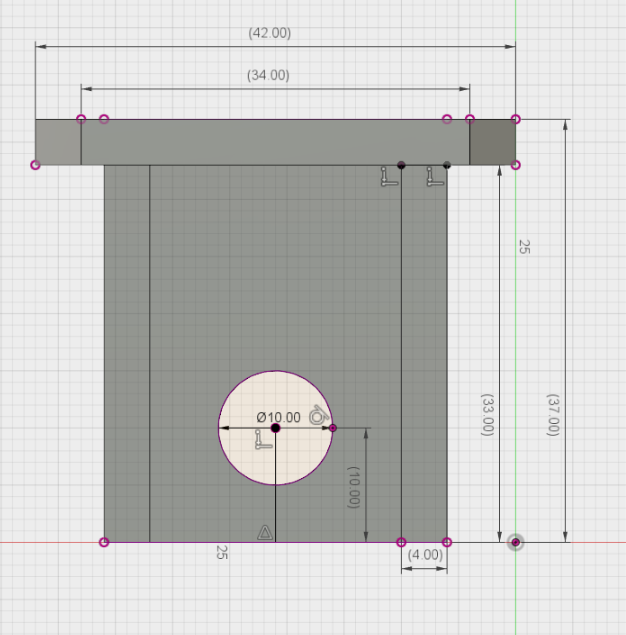
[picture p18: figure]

## Motor Platter Assembly

- Platter support assembly to 3D capture bay

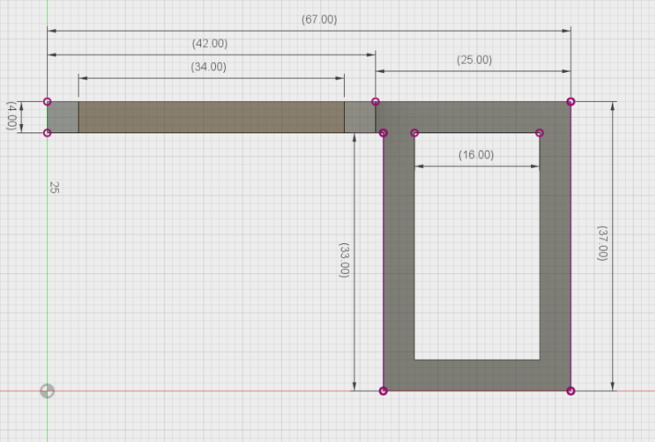
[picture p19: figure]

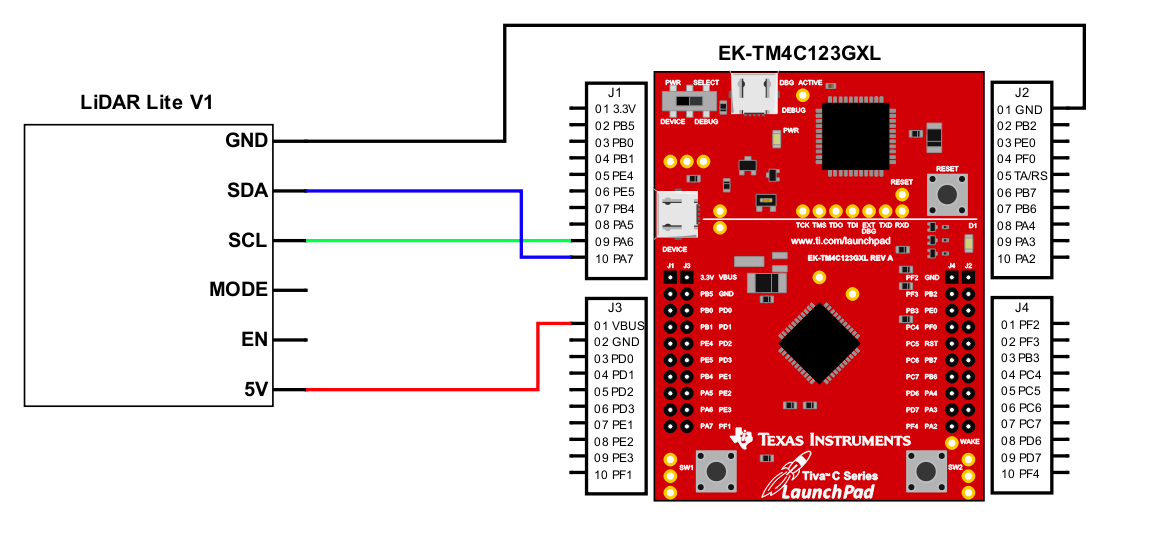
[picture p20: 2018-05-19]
Electrical/2D Assembly/Pinouts/LiDAR-Launchpad_Pinout.png

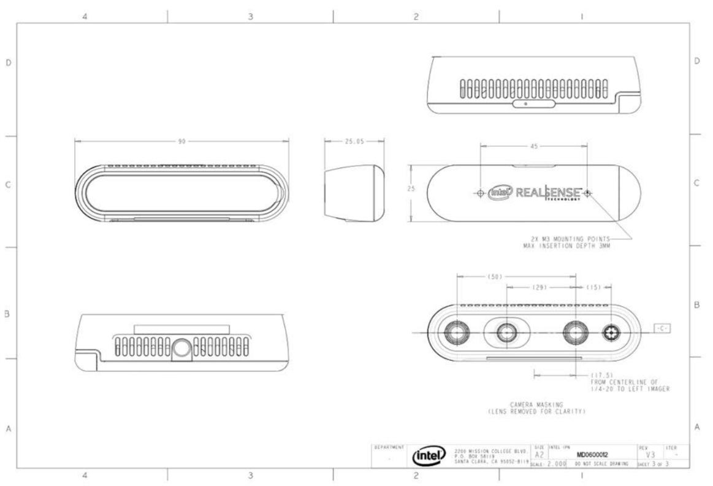
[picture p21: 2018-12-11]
Mechanical/Intel RealSense/RealSense Dimensions.png

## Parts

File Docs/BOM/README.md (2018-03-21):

# Bill of Materials
Documents the parts used in the design, and their total cost.

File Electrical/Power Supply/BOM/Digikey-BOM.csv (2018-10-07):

# | Quantity | Part Number | Manufacturer Part Number | Description | Customer Reference | Backorder | Unit Price | Extended Price
1 | 10 | P464FCT-ND | ERJ-8ENF4640V | RES SMD 464 OHM 1% 1/4W 1206 |  | 0 | 0.09700 | 0.97
2 | 10 | P715FCT-ND | ERJ-8ENF7150V | RES SMD 715 OHM 1% 1/4W 1206 |  | 0 | 0.09700 | 0.97
3 | 10 | 1276-5742-1-ND | RC3216F103CS | RES SMD 10K OHM 1% 1/4W 1206 |  | 0 | 0.08300 | 0.83
4 | 10 | 541-37.4KFCT-ND | CRCW120637K4FKEA | RES SMD 37.4K OHM 1% 1/4W 1206 |  | 0 | 0.07500 | 0.75
5 | 10 | 541-130KFCT-ND | CRCW1206130KFKEA | RES SMD 130K OHM 1% 1/4W 1206 |  | 0 | 0.07500 | 0.75
6 | 10 | 541-665KFCT-ND | CRCW1206665KFKEA | RES SMD 665K OHM 1% 1/4W 1206 |  | 0 | 0.07500 | 0.75
7 | 10 | 478-10233-1-ND | 06031U220FAT2A | CAP CER 22PF 100V NP0 0603 |  | 0 | 0.25300 | 2.53
8 | 10 | 478-6205-1-ND | 06035C222JAT2A | CAP CER 2200PF 50V X7R 0603 |  | 0 | 0.08500 | 0.85
9 | 4 | PCE3485CT-ND | EEV-FK1J471M | CAP ALUM 470UF 20% 63V SMD |  | 0 | 2.08000 | 8.32
10 | 4 | 641-1126-1-ND | CDBC540-G | DIODE SCHOTTKY 40V 5A DO214AB |  | 0 | 0.74000 | 2.96
11 | 4 | SRP1770TA-101MCT-ND | SRP1770TA-101M | FIXED IND 100UH 5.3A 118 MOHM |  | 0 | 4.10000 | 16.40
12 | 2 | 497-3468-1-ND | LD29150DT50R | IC REG LINEAR 5V 1.5A DPAK |  | 0 | 1.02000 | 2.04
13 | 10 | 478-1360-1-ND | 08051C223KAT2A | CAP CER 0.022UF 100V X7R 0805 |  | 0 | 0.11200 | 1.12
14 | 20 | 1276-1248-1-ND | CL21A475KBQNNNE | CAP CER 4.7UF 50V X5R 0805 |  | 0 | 0.30900 | 6.18
15 | 20 | PCE3946CT-ND | EEE-1JA470UP | CAP ALUM 47UF 20% 63V SMD |  | 0 | 0.42600 | 8.52
16 | 10 | 1276-1015-1-ND | CL21B103KBANNNC | CAP CER 10000PF 50V X7R 0805 |  | 0 | 0.04300 | 0.43
17 | 100 | 478-5778-1-ND | 06035C104JAT2A | CAP CER 0.1UF 50V X7R 0603 |  | 0 | 0.09400 | 9.40
18 | 10 | CR1206-FX-51R1ELFCT-ND | CR1206-FX-51R1ELF | RES SMD 51.1 OHM 1% 1/4W 1206 |  | 0 | 0.09400 | 0.94

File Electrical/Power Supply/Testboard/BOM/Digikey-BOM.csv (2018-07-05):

Index | Quantity | Part Number | Manufacturer Part Number | Description | Customer Reference | Backorder | Unit Price | Extended Price
1 | 10 | 296-40801-1-ND | TPS54531DDAR | IC REG BUCK ADJ 5A 8SOPWRPAD |  | 0 | 1.801 | $18.01
2 | 2 | 641-1419-1-ND | SB540E-G | DIODE SCHOTTKY 40V 5A DO201AD |  | 0 | 0.46 | $0.92
3 | 10 | RNF14FTD51R1CT-ND | RNF14FTD51R1 | RES 51.1 OHM 1/4W 1% AXIAL |  | 0 | 0.072 | $0.72
4 | 10 | RNF14FTD464RCT-ND | RNF14FTD464R | RES 464 OHM 1/4W 1% AXIAL |  | 0 | 0.072 | $0.72
5 | 10 | RNF14FTD10K0CT-ND | RNF14FTD10K0 | RES 10K OHM 1/4W 1% AXIAL |  | 0 | 0.072 | $0.72
6 | 10 | RNF14FTD130KCT-ND | RNF14FTD130K | RES 130K OHM 1/4W 1% AXIAL |  | 0 | 0.072 | $0.72
7 | 10 | 665KXBK-ND | MFR-25FBF52-665K | RES 665K OHM 1/4W 1% AXIAL |  | 0 | 0.082 | $0.82
8 | 10 | 37.4KXBK-ND | MFR-25FBF52-37K4 | RES 37.4K OHM 1/4W 1% AXIAL |  | 0 | 0.082 | $0.82
9 | 10 | BC2675CT-ND | K222K10X7RF5UH5 | CAP CER 2200PF 50V X7R RADIAL |  | 0 | 0.126 | $1.26
10 | 10 | BC2662CT-ND | K103K10X7RF5UH5 | CAP CER 10000PF 50V X7R RADIAL |  | 0 | 0.127 | $1.27
11 | 10 | BC1005CT-ND | K220J15C0GF5TL2 | CAP CER 22PF 50V C0G/NP0 RADIAL |  | 0 | 0.152 | $1.52
12 | 10 | P19613CT-ND | EEU-EB1H470SH | CAP ALUM 47UF 20% 50V RADIAL |  | 0 | 0.243 | $2.43
13 | 10 | P15839CT-ND | EEA-GA1H4R7H | CAP ALUM 4.7UF 20% 50V RADIAL |  | 0 | 0.167 | $1.67
14 | 2 | M8803-ND | 2103-H-RC | FIXED IND 15UH 7.7A 12 MOHM TH |  | 0 | 2.5 | $5.00
15 | 10 | 1.96KXBK-ND | MFR-25FBF52-1K96 | RES 1.96K OHM 1/4W 1% AXIAL |  | 0 | 0.082 | $0.82
16 | 10 | 715XBK-ND | MFR-25FBF52-715R | RES 715 OHM 1/4W 1% AXIAL |  | 0 | 0.082 | $0.82
 |  |  |  |  |  |  | Subtotal | $38.24

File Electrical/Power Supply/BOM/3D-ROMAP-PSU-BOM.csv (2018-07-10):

# | Qty | Value | Manufacturer | Part Number | Reference
1 | 4 | 470uF | Panasonic | EEV-FK1J471M | C1 C2 C3 C4
2 | 13 | 0.1uF | KEMET | C0603C104K5RACAUTO | C5 C7 C9 C11 C13 C14 C15 C18 C21 C34 C35 C38 C41
3 | 9 | 4.7uF | Panasonic | CL21A475KBQNNNE | C6 C10 C22 C23 C26 C42 C43 C45 C46
4 | 10 | 47uF | Panasonic | EEE-1JA470UP | C8 C12 C16 C17 C19 C20 C36 C37 C39 C40
5 | 4 | 0.01uF | Samsung | CL21B103KBANNNC | C24 C27 C44 C47
6 | 1 | 4.7uF | Samsung | CL21A475KBQNNNE | C25
7 | 4 | 2200pF | AVX Corp | 06035C222JAT2A | C28 C29 C48 C49
8 | 4 | 22pF | AVX Corp | 06031U220FAT2A | C30 C31 C50 C51
9 | 4 | 0.022uF | AVX Corp | 08051C223KAT2A | C32 C33 C52 C53
10 | 4 | Schottky | Comchip Technology | CDBC540-G | D1 D2 D3 D4
11 | 7 | Conn-2 | Generic | Terminal-2pin | J1 J2 J3 J4 J5 J6 J7
12 | 4 | 100uH | Bourns Inc. | SRP1770TA-101M | L1 L2 L3 L4
13 | 4 | 51.1 | Vishay Dale | CRCW120651R1FKEA | R1 R2 R13 R14
14 | 4 | 665k | Vishay Dale | CRCW1206665KFKEA | R3 R4 R15 R16
15 | 4 | 10k | Samsung | RC3216F103CS | R5 R6 R17 R18
16 | 4 | 130k | Vishay Dale | CRCW1206130KFKEA | R7 R9 R19 R21
17 | 4 | 37.4k | Vishay Dale | CRCW120637K4FKEA | R8 R10 R20 R22
18 | 1 | 464 | Vishay Dale | CRCW1206130KFKEA | R11
19 | 3 | 715 | Panasonic | ERJ-8ENF7150V | R12 R23 R24
20 | 2 | LD29150 | STMicroelectronics | LD29150DT50R | U1 U2
21 | 4 | TPS54531 | Texas Instruments | TPS54531DDAR | U3 U4 U5 U6

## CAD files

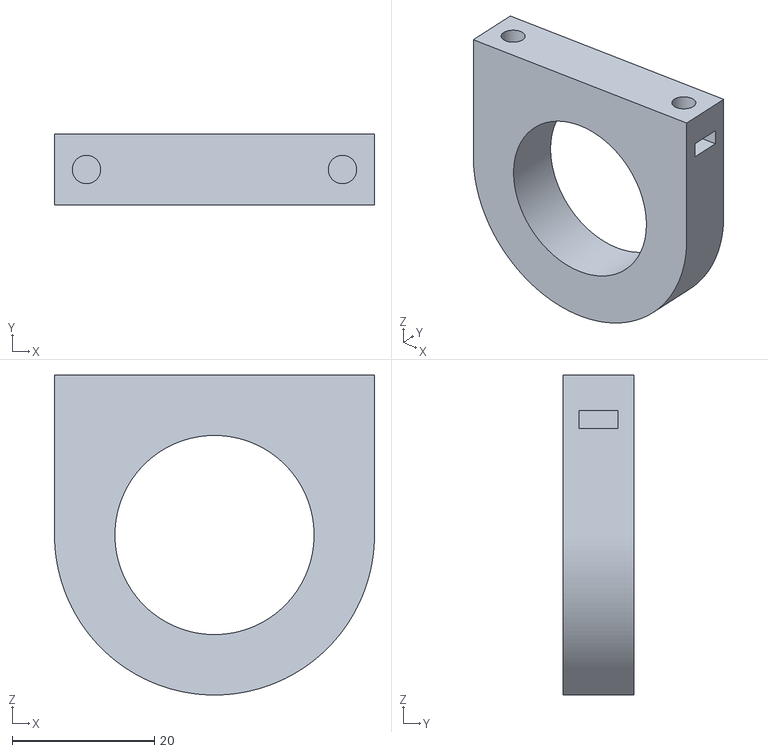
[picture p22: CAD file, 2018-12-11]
Mechanical/Chassis Components/3D Printed Parts/Movement Motor Back Mount.stl
45.0 x 10.0 x 45.0

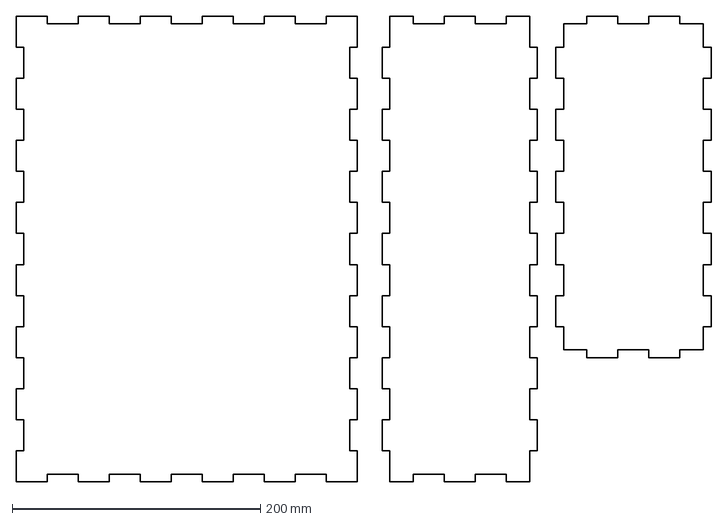
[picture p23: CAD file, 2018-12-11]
Mechanical/Chassis Components/3DROMAP_Chassis/3DROMAP_Chassis.dxf
560.0 x 375.0 mm

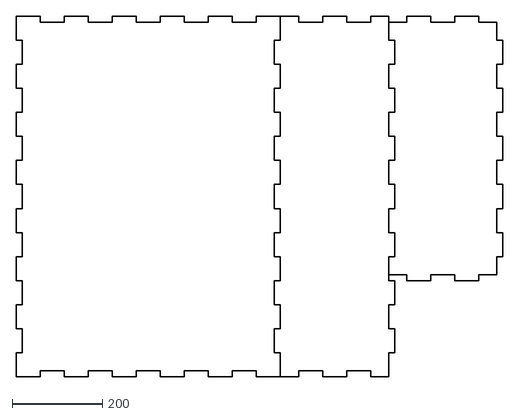
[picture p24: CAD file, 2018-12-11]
Mechanical/Chassis Components/3DROMAP_Chassis_Condensed/3DROMAP_Chassis_condensed.dxf
1076.6 x 797.2

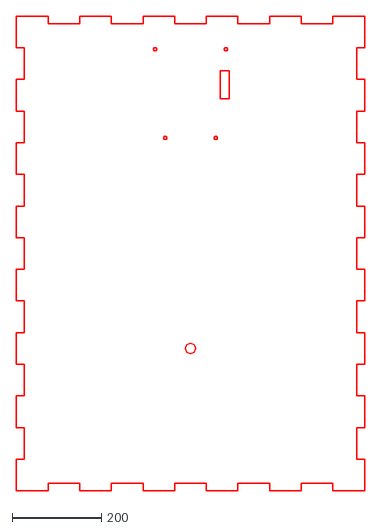
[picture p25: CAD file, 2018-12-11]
Mechanical/Chassis Components/3DROMAP_Chassis_Top_with_Mounting_Holes/3DROMAP_Chassis_Top_with_Mounting_Holes.dxf
778.8 x 1062.2

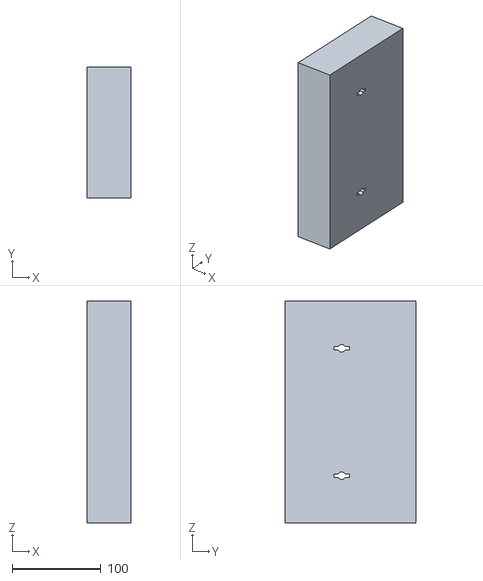
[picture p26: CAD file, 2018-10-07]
Mechanical/Physical Components/Router.stl
50.0 x 147.5 x 250.0

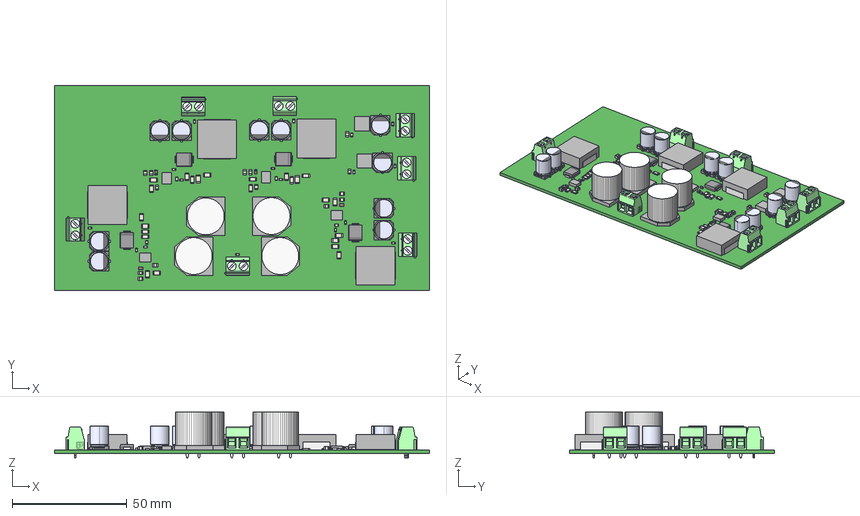
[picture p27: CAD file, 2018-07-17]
Mechanical/Power Supply Assembly/3D-ROMAP-PSU.step
163.1 x 89.2 x 20.0 mm
Board
Extruded x 203
User_Library-AL_EL_cap_8mmx10mm_foot_cap_8x8_1 x 20
User_Library-AL_EL_cap_8mmx10mm_can_8x8_1 x 10
User_Library-AL_EL_cap_8mmx10mm_alelcap_sm8x8_1 x 10
User_Library-CapCeramic_Kemet_0805_2012 x 4
mkdsn_1.5-2-5.08 x 7
DO-214AB_SMC x 4

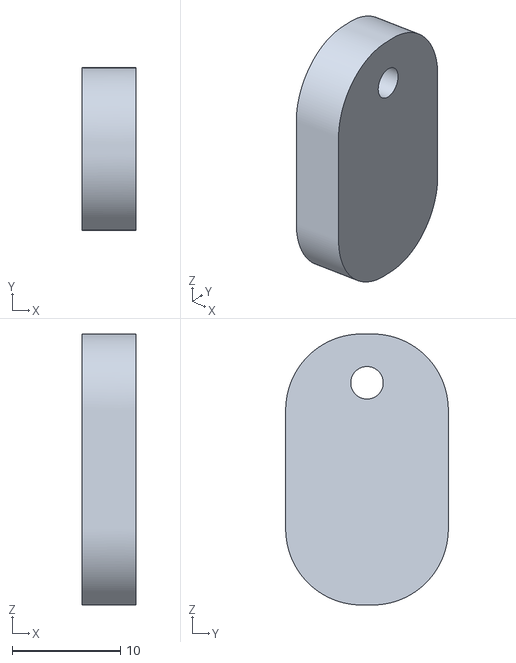
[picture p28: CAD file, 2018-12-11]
Mechanical/Chassis Components/3D Printed Parts/Face Clip.stl
5.00 x 15.0 x 25.0

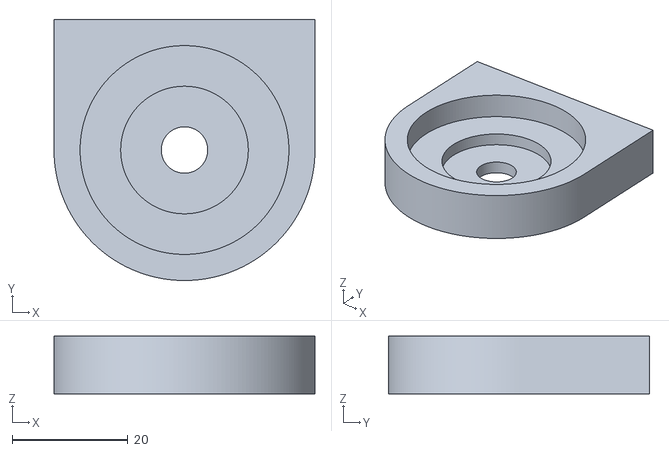
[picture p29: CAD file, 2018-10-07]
Mechanical/Physical Components/MMount1.stl
45.0 x 45.0 x 10.0

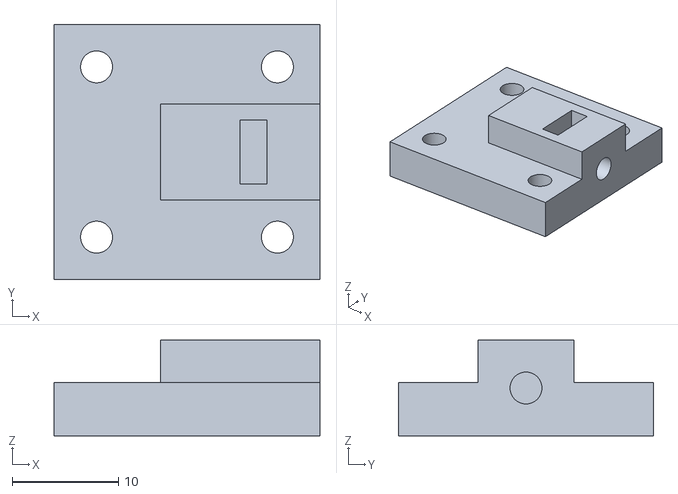
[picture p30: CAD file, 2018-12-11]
Mechanical/Chassis Components/3D Printed Parts/Face Clip Mount.stl
25.0 x 24.0 x 9.00

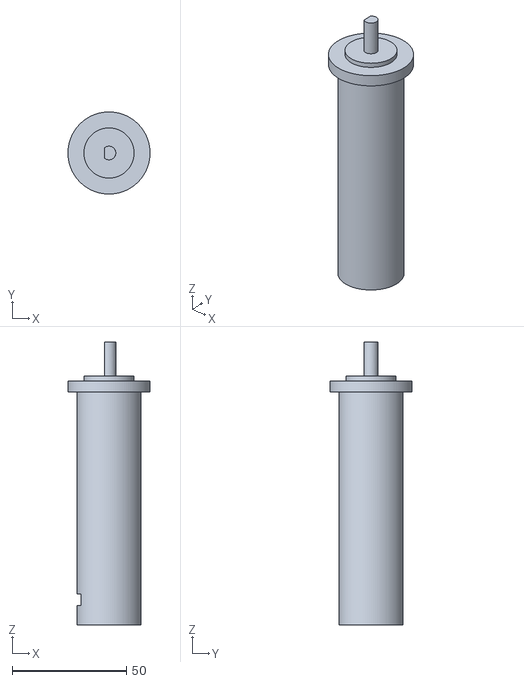
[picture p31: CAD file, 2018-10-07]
Mechanical/Physical Components/Motor2.stl
36.0 x 36.0 x 124.0

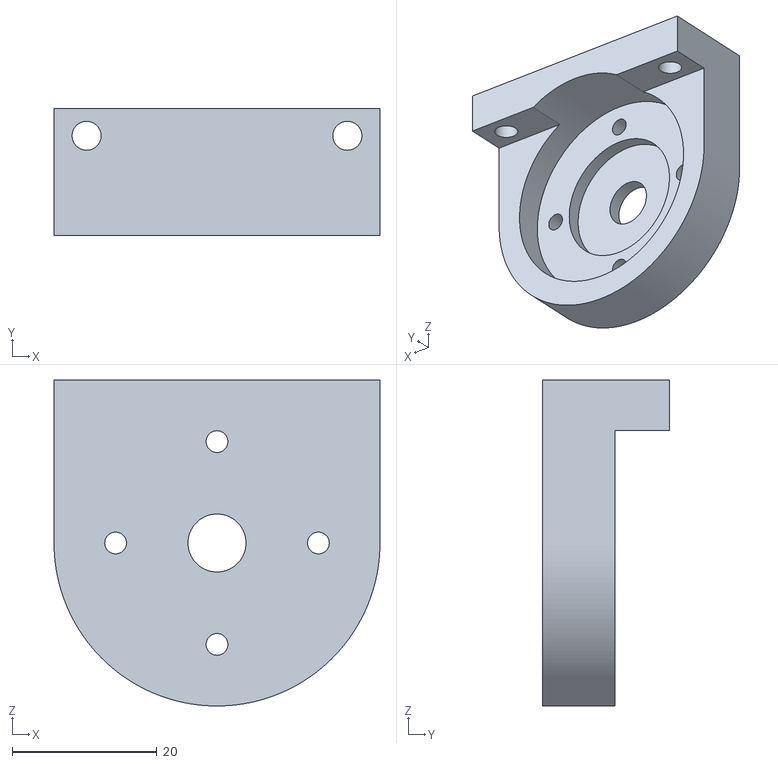
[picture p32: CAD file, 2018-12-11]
Mechanical/Chassis Components/3D Printed Parts/Movement Motor Mount.stl
45.0 x 17.5 x 45.0

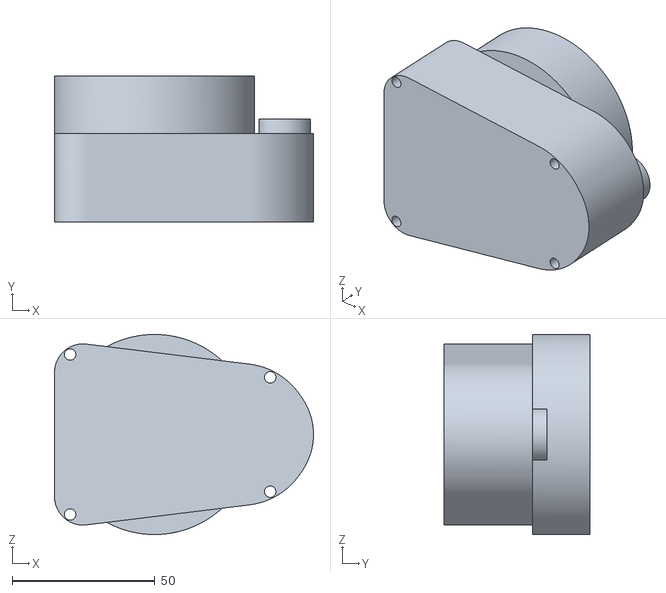
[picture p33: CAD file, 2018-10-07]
Mechanical/Physical Components/RPLidar.stl
90.6 x 51.0 x 70.0

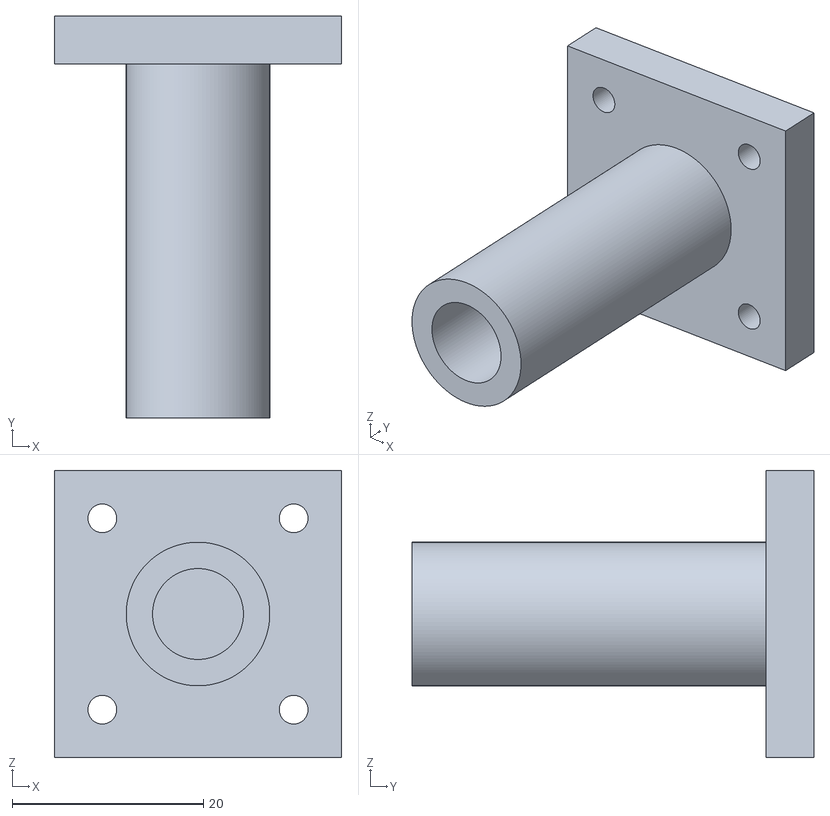
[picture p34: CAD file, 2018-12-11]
Mechanical/Chassis Components/3D Printed Parts/Caster Mount.stl
30.0 x 42.0 x 30.0

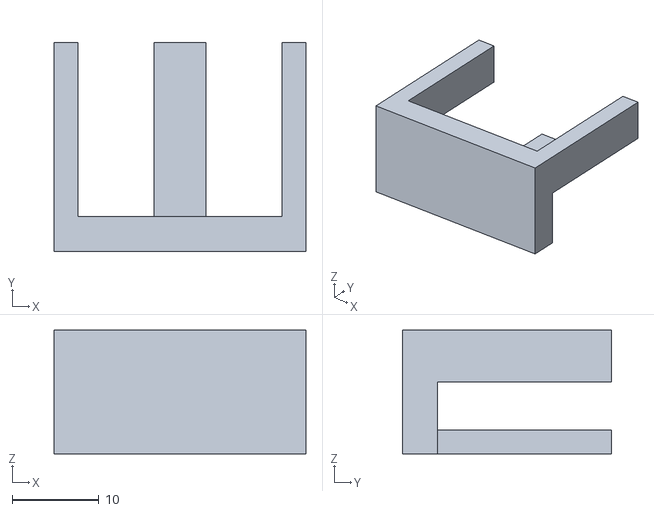
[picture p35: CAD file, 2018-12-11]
Mechanical/Chassis Components/3D Printed Parts/Battery Mount v2.stl
29.0 x 24.0 x 14.2

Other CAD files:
Software/PCL-Realsense-Capture/RS_Testing/Captured_Frame.ply
Mechanical/Physical Components/Motor1.stl
Mechanical/Physical Components/Jetson.stl
Mechanical/Chassis Components/3D Printed Parts/RealSense Mount.stl
Mechanical/Chassis Components/Completed Assembly/Work Area.f3d
Mechanical/Physical Components/ARM.stl
Mechanical/Physical Components/MMount2.stl
Mechanical/Physical Components/PowerSupply.stl
Mechanical/Physical Components/RealSense.stl
Mechanical/Physical Components/Wheel1.stl
Mechanical/Physical Components/Wheel2.stl

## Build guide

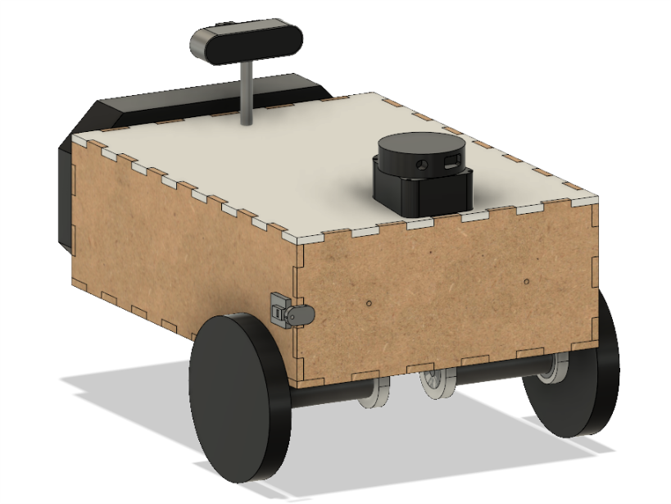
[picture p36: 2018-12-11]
Mechanical/Chassis Components/Completed Assembly/Completed_Assembly.png

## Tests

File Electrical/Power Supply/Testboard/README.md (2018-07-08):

# Power Supply - Test Board
  DCDC buck converter test board with 5v and 12v tests.

  Tested with the following resistance values:
  * 5v -> 1.96k
  * 12v -> 714

  Approximate voltage is 4.9v and 12v, due to lower resistor value for 5v.

## Noise
  Upon testing, an approximate 1Vpp is detected due to low inductance.  This
  has been tested via analysis and inspection.

  The 12v router supply will be shared with a 5v LDO to increase current draw,
  lower cost, and lower the minimum inductor value.
  
  Testing has prompted design change to use a larger inductor on sources, and
  5v LDO source to reduce ripple.

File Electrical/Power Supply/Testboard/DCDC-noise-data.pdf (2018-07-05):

Scope Data

X | CH1 | Start | Increment Vavg Vmax Vmin Vswing Max
Sequence Volt -0.0003 | 5E-07 | 4.9 | 5.4 | 4.5 | 0.92
0 | 4.92
1 | 4.88
2 | 4.88
3 | 4.92
4 | 4.92
5 | 4.88
6 | 4.88
7 | 4.92
8 | 4.92
9 | 4.88
10 | 4.92
11 | 4.88
12 | 4.92
13 | 4.88
14 | 4.92
15 | 4.88
16 | 4.92
17 | 4.88
18 | 4.92
19 | 4.88
20 | 4.88
21 | 4.92
22 | 4.88
23 | 4.92
24 | 4.88
25 | 4.92
26 | 4.92
27 | 4.88
28 | 4.92
29 | 4.88
30 | 4.88
31 | 4.92
32 | 4.88
33 | 4.92
34 | 4.92
35 | 4.88
36 | 4.88
37 | 4.92
38 | 4.92
39 | 4.88
40 | 4.92
41 | 4.88
42 | 4.92
43 | 4.88
44 | 4.92
45 | 4.88
46 | 4.92
47 | 4.88
48 | 4.88
49 | 4.92
50 | 4.92
51 | 4.88
52 | 4.88
53 | 4.92
54 | 4.88
55 | 4.92
56 | 4.92
57 | 4.88
58 | 4.92
59 | 4.88
60 | 4.92
61 | 4.88
62 | 4.88
63 | 4.92

Page

64 | 4.92
65 | 4.88
66 | 4.92
67 | 4.88
68 | 4.92
69 | 4.88
70 | 4.92
71 | 4.88
72 | 4.92
73 | 4.88
74 | 4.92
75 | 4.88
76 | 4.92
77 | 4.88
78 | 4.92
79 | 4.88
80 | 4.92
81 | 4.88
82 | 4.92
83 | 4.88
84 | 4.88
85 | 4.92
86 | 4.88
87 | 4.92
88 | 4.88
89 | 4.92
90 | 4.88
91 | 4.92
92 | 4.92
93 | 4.88
94 | 4.88
95 | 4.92
96 | 4.92
97 | 4.88
98 | 4.92
99 | 4.88
100 | 4.92
101 | 4.88
102 | 4.88
103 | 4.92
104 | 4.92
105 | 4.88
106 | 4.92
107 | 4.88
108 | 4.92
109 | 4.88
110 | 4.92
111 | 4.88
112 | 4.88
113 | 4.92
114 | 4.92
115 | 4.88
116 | 4.92
117 | 4.88
118 | 4.92
119 | 4.88
120 | 4.88
121 | 4.92
122 | 4.92
123 | 4.88
124 | 4.92
125 | 4.88
126 | 4.92
127 | 4.88
128 | 4.88
129 | 4.92

131 | 4.88
132 | 4.92
133 | 4.88
134 | 4.92
135 | 4.88
136 | 4.88
137 | 4.92
138 | 4.88
139 | 4.92
140 | 4.92
141 | 4.88
142 | 4.88
143 | 4.92
144 | 4.92
145 | 4.88
146 | 4.88
147 | 4.92
148 | 4.92
149 | 4.88
150 | 4.92
151 | 4.88
152 | 4.88
153 | 4.92
154 | 4.92
155 | 4.88
156 | 4.92
157 | 4.88
158 | 4.88
159 | 4.92
160 | 4.92
161 | 4.88
162 | 4.92
163 | 4.88
164 | 4.92
165 | 4.88
166 | 4.92
167 | 4.88
168 | 4.92
169 | 4.88
170 | 4.88
171 | 4.92
172 | 4.92
173 | 4.88
174 | 4.92
175 | 4.88
176 | 4.88
177 | 4.92
178 | 4.88
179 | 4.92
180 | 4.92
181 | 4.88
182 | 4.88
183 | 4.92
184 | 4.92
185 | 4.88
186 | 4.92
187 | 4.88
188 | 4.92
189 | 4.88
190 | 4.92
191 | 4.88
192 | 4.88
193 | 4.92
194 | 4.88
195 | 4.92

197 | 4.88
198 | 4.92
199 | 4.88
200 | 4.92
201 | 4.88
202 | 4.92
203 | 4.88
204 | 4.92
205 | 4.88
206 | 4.88
207 | 4.92
208 | 4.92
209 | 4.88
210 | 4.92
211 | 4.88
212 | 4.92
213 | 4.88
214 | 4.92
215 | 4.88
216 | 4.88
217 | 4.92
218 | 4.92
219 | 4.88
220 | 4.88
221 | 4.92
222 | 4.92
223 | 4.88
224 | 4.92
225 | 4.88
226 | 4.92
227 | 4.88
228 | 4.92
229 | 4.88
230 | 4.88
231 | 4.92
232 | 4.92
233 | 4.88
234 | 4.88
235 | 4.92
236 | 4.92
237 | 4.88
238 | 4.92
239 | 4.88
240 | 4.92
241 | 4.88
242 | 4.92
243 | 4.88
244 | 4.88
245 | 4.92
246 | 4.92
247 | 4.88
248 | 4.88
249 | 4.92
250 | 4.92
251 | 4.88
252 | 4.92
253 | 4.88
254 | 4.92
255 | 4.88
256 | 4.88
257 | 4.92
258 | 4.92
259 | 4.88
260 | 4.92
261 | 4.88

263 | 4.88
264 | 4.88
265 | 4.92
266 | 4.92
267 | 4.88
268 | 4.88
269 | 4.92
270 | 4.88
271 | 4.92
272 | 4.92
273 | 4.88
274 | 4.92
275 | 4.88
276 | 4.92
277 | 4.88
278 | 4.92
279 | 4.88
280 | 4.92
281 | 4.88
282 | 4.92
283 | 4.88
284 | 4.92
285 | 4.88
286 | 4.92
287 | 4.88
288 | 4.88
289 | 4.92
290 | 4.92
291 | 4.88
292 | 4.92
293 | 4.88
294 | 4.92
295 | 4.88
296 | 4.88
297 | 4.92
298 | 4.88
299 | 4.92
300 | 4.92
301 | 4.88
302 | 4.92
303 | 4.88
304 | 4.92
305 | 4.88
306 | 4.92
307 | 4.88
308 | 4.88
309 | 4.92
310 | 4.92
311 | 4.88
312 | 4.88
313 | 4.92
314 | 4.88
315 | 4.92
316 | 4.88
317 | 4.92
318 | 4.92
319 | 4.88
320 | 4.92
321 | 4.88
322 | 4.92
323 | 4.88
324 | 4.88
325 | 4.92
326 | 4.92
327 | 4.88

329 | 4.92
330 | 4.92
331 | 4.88
332 | 4.92
333 | 4.88
334 | 4.92
335 | 4.88
336 | 4.92
337 | 4.88
338 | 4.92
339 | 4.88
340 | 4.88
341 | 4.92
342 | 4.92
343 | 4.88
344 | 4.92
345 | 4.88
346 | 4.92
347 | 4.88
348 | 4.88
349 | 4.92
350 | 4.92
351 | 4.88
352 | 4.92
353 | 4.88
354 | 4.92
355 | 4.88
356 | 4.88
357 | 4.92
358 | 4.88
359 | 4.92
360 | 4.88
361 | 4.92
362 | 4.92
363 | 4.88
364 | 4.92
365 | 4.88
366 | 4.92
367 | 4.88
368 | 4.92
369 | 4.88
370 | 4.92
371 | 4.88
372 | 4.92
373 | 4.88
374 | 4.92
375 | 4.88
376 | 4.92
377 | 4.88
378 | 4.92
379 | 4.88
380 | 4.92
381 | 4.88
382 | 4.92
383 | 4.88
384 | 4.92
385 | 4.88
386 | 4.88
387 | 4.92
388 | 4.92
389 | 4.88
390 | 4.92
391 | 4.88
392 | 4.88
393 | 4.92

395 | 4.88
396 | 4.92
397 | 4.88
398 | 4.92
399 | 4.88
400 | 4.92
401 | 4.88
402 | 4.88
403 | 4.92
404 | 4.88
405 | 4.92
406 | 4.92
407 | 4.88
408 | 4.88
409 | 4.92
410 | 4.88
411 | 4.92
412 | 4.92
413 | 4.88
414 | 4.92
415 | 4.88
416 | 4.88
417 | 4.92
418 | 4.92
419 | 4.88
420 | 4.92
421 | 4.88
422 | 4.92
423 | 4.88
424 | 4.92
425 | 4.88
426 | 4.92
427 | 4.88
428 | 4.88
429 | 4.92
430 | 4.88
431 | 4.92
432 | 4.92
433 | 4.88
434 | 4.92
435 | 4.88
436 | 4.88
437 | 4.92
438 | 4.92
439 | 4.88
440 | 4.92
441 | 4.88
442 | 4.92
443 | 4.88
444 | 4.92
445 | 4.88
446 | 4.92
447 | 4.88
448 | 4.88
449 | 4.92
450 | 4.92
451 | 4.88
452 | 4.92
453 | 4.88
454 | 4.92
455 | 4.88
456 | 4.92
457 | 4.88
458 | 4.92
459 | 4.88

461 | 4.92
462 | 4.88
463 | 4.92
464 | 4.92
465 | 4.88
466 | 4.88
467 | 4.92
468 | 4.92
469 | 4.88
470 | 4.88
471 | 4.92
472 | 4.92
473 | 4.88
474 | 4.92
475 | 4.88
476 | 4.92
477 | 4.88
478 | 4.92
479 | 4.88
480 | 4.92
481 | 4.88
482 | 4.92
483 | 4.88
484 | 4.92
485 | 4.88
486 | 4.92
487 | 4.88
488 | 4.92
489 | 4.88
490 | 4.92
491 | 4.88
492 | 4.92
493 | 4.88
494 | 4.92
495 | 4.88
496 | 4.92
497 | 4.88
498 | 4.92
499 | 4.88
500 | 4.88
501 | 4.92
502 | 4.92
503 | 4.88
504 | 4.88
505 | 4.92
506 | 4.88
507 | 4.92
508 | 4.92
509 | 4.88
510 | 4.92
511 | 4.88
512 | 4.92
513 | 4.88
514 | 4.88
515 | 4.92
516 | 4.92
517 | 4.88
518 | 4.92
519 | 4.88
520 | 4.88
521 | 4.92
522 | 4.92
523 | 4.88
524 | 4.88
525 | 4.92

527 | 4.92
528 | 4.88
529 | 4.92
530 | 4.92
531 | 4.88
532 | 4.92
533 | 4.88
534 | 4.92
535 | 4.88
536 | 4.92
537 | 4.88
538 | 4.92
539 | 4.88
540 | 4.92
541 | 4.88
542 | 4.92
543 | 4.88
544 | 4.88
545 | 4.92
546 | 4.92
547 | 4.88
548 | 4.88
549 | 4.92
550 | 4.92
551 | 4.88
552 | 4.92
553 | 4.88
554 | 4.92
555 | 4.88
556 | 4.92
557 | 4.88
558 | 4.92
559 | 4.88
560 | 4.92
561 | 4.88
562 | 4.92
563 | 4.88
564 | 4.92
565 | 4.88
566 | 4.92
567 | 4.88
568 | 4.92
569 | 4.88
570 | 4.88
571 | 4.92
572 | 4.92
573 | 4.88
574 | 4.92
575 | 4.88
576 | 4.92
577 | 4.88
578 | 4.92
579 | 4.88
580 | 4.92
581 | 4.88
582 | 4.92
583 | 4.88
584 | 4.92
585 | 4.88
586 | 4.92
587 | 4.88
588 | 4.92
589 | 4.88
590 | 4.92
591 | 4.88

593 | 4.88
594 | 4.92
595 | 4.88
596 | 4.92
597 | 4.88
598 | 4.96
599 | 4.68
600 | 5.2
601 | 4.64
602 | 4.72
603 | 5.24
604 | 4.96
605 | 4.84
606 | 5.2
607 | 4.56
608 | 4.96
609 | 4.88
610 | 4.68
611 | 5.24
612 | 4.92
613 | 4.88
614 | 5.24
615 | 4.52
616 | 4.88
617 | 4.92
618 | 5.24
619 | 4.52
620 | 5.4
621 | 4.52
622 | 4.76
623 | 5
624 | 4.72
625 | 5.24
626 | 4.84
627 | 4.96
628 | 5.2
629 | 4.56
630 | 4.92
631 | 4.88
632 | 5.4
633 | 4.52
634 | 4.88
635 | 4.92
636 | 4.68
637 | 5.2
638 | 4.88
639 | 4.92
640 | 5.24
641 | 4.52
642 | 4.48
643 | 5.32
644 | 5
645 | 4.84
646 | 4.68
647 | 5.24
648 | 4.96
649 | 4.84
650 | 4.48
651 | 5.32
652 | 4.88
653 | 4.92
654 | 4.76
655 | 5.24
656 | 4.92
657 | 4.88

658 | 5.24
659 | 4.6
660 | 4.92
661 | 4.88
662 | 4.48
663 | 5.36
664 | 4.68
665 | 5.24
666 | 4.88
667 | 5
668 | 5.24
669 | 4.64
670 | 4.84
671 | 4.92
672 | 4.48
673 | 5.32
674 | 4.88
675 | 4.92
676 | 4.84
677 | 5.24
678 | 4.92
679 | 4.88
680 | 5.16
681 | 4.56
682 | 4.48
683 | 5.32
684 | 5.24
685 | 4.68
686 | 4.68
687 | 5.2
688 | 4.96
689 | 4.84
690 | 5.24
691 | 4.52
692 | 4.96
693 | 4.84
694 | 4.48
695 | 5.4
696 | 4.92
697 | 4.88
698 | 4.72
699 | 5.24
700 | 4.92
701 | 4.88
702 | 4.56
703 | 5.2
704 | 4.48
705 | 5.36
706 | 5.2
707 | 4.76
708 | 5.24
709 | 4.64
710 | 4.88
711 | 4.96
712 | 4.48
713 | 5.36
714 | 4.88
715 | 4.92
716 | 4.8
717 | 5.24
718 | 4.88
719 | 4.92
720 | 5.24
721 | 4.6
722 | 4.92
723 | 4.88

725 | 5.36
726 | 4.72
727 | 5.24
728 | 4.84
729 | 5.04
730 | 5.24
731 | 4.52
732 | 4.96
733 | 4.84
734 | 5.24
735 | 4.52
736 | 4.88
737 | 4.96
738 | 5.24
739 | 4.64
740 | 4.92
741 | 4.88
742 | 4.48
743 | 5.4
744 | 4.92
745 | 4.88
746 | 4.68
747 | 5.24
748 | 5.24
749 | 4.52
750 | 4.96
751 | 4.84
752 | 4.48
753 | 5.4
754 | 4.96
755 | 4.84
756 | 4.72
757 | 5.24
758 | 4.88
759 | 4.96
760 | 5.24
761 | 4.64
762 | 4.92
763 | 4.88
764 | 4.48
765 | 5.32
766 | 4.88
767 | 5.24
768 | 4.52
769 | 5.24
770 | 4.68
771 | 5.2
772 | 4.96
773 | 4.84
774 | 4.48
775 | 5.4
776 | 4.88
777 | 4.96
778 | 4.76
779 | 5.24
780 | 4.88
781 | 4.96
782 | 5.2
783 | 4.56
784 | 4.88
785 | 4.96
786 | 4.48
787 | 5.32
788 | 4.68
789 | 5.24

790 | 5.04
791 | 4.8
792 | 4.68
793 | 5.24
794 | 4.96
795 | 4.84
796 | 5.28
797 | 4.52
798 | 4.88
799 | 4.96
800 | 4.48
801 | 5.32
802 | 4.88
803 | 4.96
804 | 5.36
805 | 4.52
806 | 4.88
807 | 4.96
808 | 4.76
809 | 5.24
810 | 4.68
811 | 5.24
812 | 5.08
813 | 4.84
814 | 5.24
815 | 4.64
816 | 4.96
817 | 4.84
818 | 4.56
819 | 5.28
820 | 4.88
821 | 4.96
822 | 4.48
823 | 5.36
824 | 4.88
825 | 4.96
826 | 5.4
827 | 4.52
828 | 4.88
829 | 4.96
830 | 5.2
831 | 4.68
832 | 4.68
833 | 5.2
834 | 4.84
835 | 5.04
836 | 4.68
837 | 5.24
838 | 4.96
839 | 4.84
840 | 5.2
841 | 4.6
842 | 4.88
843 | 4.96
844 | 5.24
845 | 4.64
846 | 4.88
847 | 4.96
848 | 5.24
849 | 4.56
850 | 4.96
851 | 4.88
852 | 4.48
853 | 5.32
854 | 4.48
855 | 5.36

857 | 4.84
858 | 5.24
859 | 4.68
860 | 4.84
861 | 4.96
862 | 4.76
863 | 5.24
864 | 4.88
865 | 4.96
866 | 5.24
867 | 4.72
868 | 4.96
869 | 4.88
870 | 4.76
871 | 5.24
872 | 4.96
873 | 4.76
874 | 5.24
875 | 4.84
876 | 5.24
877 | 4.52
878 | 4.96
879 | 4.84
880 | 4.8
881 | 5.24
882 | 4.96
883 | 4.88
884 | 4.68
885 | 5.24
886 | 4.88
887 | 5
888 | 4.68
889 | 5.24
890 | 4.96
891 | 4.88
892 | 4.68
893 | 5.2
894 | 4.68
895 | 5.24
896 | 5.2
897 | 4.68
898 | 4.68
899 | 5.24
900 | 4.88
901 | 5
902 | 4.68
903 | 5.24
904 | 4.88
905 | 5
906 | 4.68
907 | 5.24
908 | 4.96
909 | 4.88
910 | 4.68
911 | 5.24
912 | 4.96
913 | 4.88
914 | 4.48
915 | 5.4
916 | 4.88
917 | 5
918 | 4.88
919 | 4.96
920 | 4.88
921 | 5

923 | 4.96
924 | 4.96
925 | 4.88
926 | 4.88
927 | 4.96
928 | 4.88
929 | 5
930 | 4.96
931 | 4.88
932 | 4.88
933 | 5
934 | 4.88
935 | 5
936 | 4.96
937 | 4.88
938 | 4.88
939 | 4.96
940 | 4.88
941 | 4.96
942 | 4.88
943 | 5
944 | 4.88
945 | 4.96
946 | 4.88
947 | 4.96
948 | 4.96
949 | 4.88
950 | 4.88
951 | 4.96
952 | 4.88
953 | 5
954 | 4.96
955 | 4.88
956 | 4.88
957 | 4.96
958 | 4.88
959 | 4.96
960 | 4.96
961 | 4.88
962 | 4.96
963 | 4.88
964 | 4.96
965 | 4.88
966 | 4.88
967 | 5
968 | 4.96
969 | 4.88
970 | 4.88
971 | 4.96
972 | 4.96
973 | 4.88
974 | 4.88
975 | 4.96
976 | 4.88
977 | 4.96
978 | 4.96
979 | 4.88
980 | 4.88
981 | 4.96
982 | 4.88
983 | 5
984 | 4.96
985 | 4.88
986 | 4.88
987 | 5

989 | 4.88
990 | 4.88
991 | 4.96
992 | 4.88
993 | 4.96
994 | 4.88
995 | 4.96
996 | 4.88
997 | 4.96
998 | 4.96
999 | 4.88
1000 | 4.96
1001 | 4.88
1002 | 4.88
1003 | 4.96
1004 | 4.96
1005 | 4.88
1006 | 4.88
1007 | 4.96
1008 | 4.88
1009 | 4.96
1010 | 4.88
1011 | 4.96
1012 | 4.88
1013 | 4.96
1014 | 5
1015 | 4.88
1016 | 4.96
1017 | 4.88
1018 | 4.88
1019 | 4.96
1020 | 4.96
1021 | 4.88
1022 | 4.88
1023 | 4.96
1024 | 4.96
1025 | 4.88
1026 | 4.88
1027 | 5
1028 | 4.88
1029 | 4.96
1030 | 4.96
1031 | 4.88
1032 | 4.88
1033 | 4.96
1034 | 4.88
1035 | 5
1036 | 4.96
1037 | 4.88
1038 | 4.96
1039 | 4.88
1040 | 4.96
1041 | 4.88
1042 | 4.88
1043 | 4.96
1044 | 4.96
1045 | 4.88
1046 | 4.96
1047 | 4.88
1048 | 4.88
1049 | 4.96
1050 | 4.88
1051 | 4.96
1052 | 4.88
1053 | 4.96

1055

5
1056 | 4.88
1057 | 4.96
1058 | 4.88
1059 | 4.96
1060 | 4.88
1061 | 4.96
1062 | 4.88
1063 | 4.96
1064 | 4.88
1065 | 4.96
1066 | 4.88
1067 | 4.96
1068 | 4.88
1069 | 4.96
1070 | 4.88
1071 | 4.96
1072 | 4.88
1073 | 4.96
1074 | 4.88
1075 | 5
1076 | 4.88
1077 | 4.96
1078 | 4.88
1079 | 4.96
1080 | 4.96
1081 | 4.88
1082 | 4.88
1083 | 4.96
1084 | 4.88
1085 | 5
1086 | 4.88
1087 | 4.96
1088 | 4.88
1089 | 4.96
1090 | 4.88
1091 | 4.96
1092 | 4.88
1093 | 4.96
1094 | 4.88
1095 | 5
1096 | 4.96
1097 | 4.88
1098 | 4.88
1099 | 5
1100 | 4.96
1101 | 4.88
1102 | 4.88
1103 | 4.96
1104 | 4.96
1105 | 4.88
1106 | 4.88
1107 | 4.96
1108 | 4.88
1109 | 4.96
1110 | 4.88
1111 | 4.96
1112 | 4.96
1113 | 4.88
1114 | 4.88
1115 | 5
1116 | 4.88
1117 | 5
1118 | 4.88
1119 | 4.96

1121 | 4.96
1122 | 4.96
1123 | 4.88
1124 | 4.88
1125 | 4.96
1126 | 4.88
1127 | 4.96
1128 | 4.88
1129 | 4.96
1130 | 4.88
1131 | 4.96
1132 | 4.88
1133 | 4.96
1134 | 4.88
1135 | 4.96
1136 | 4.88
1137 | 4.96
1138 | 4.88
1139 | 4.96
1140 | 5
1141 | 4.88
1142 | 4.88
1143 | 4.96
1144 | 4.88
1145 | 4.96
1146 | 4.88
1147 | 4.96
1148 | 4.88
1149 | 4.96
1150 | 4.88
1151 | 5
1152 | 4.88
1153 | 4.96
1154 | 4.88
1155 | 4.96
1156 | 4.88
1157 | 4.96
1158 | 4.88
1159 | 4.96
1160 | 4.88
1161 | 4.96
1162 | 4.88
1163 | 4.96
1164 | 4.96
1165 | 4.88
1166 | 4.88
1167 | 4.96
1168 | 4.88
1169 | 4.96
1170 | 4.88
1171 | 4.96
1172 | 4.96
1173 | 4.88
1174 | 4.96
1175 | 4.88
1176 | 4.96
1177 | 4.88
1178 | 4.88
1179 | 4.96
1180 | 4.96
1181 | 4.88
1182 | 4.96
1183 | 4.88
1184 | 4.88
1185 | 4.96

1187 | 4.96
1188 | 4.88
1189 | 4.96
1190 | 4.88
1191 | 4.96
1192 | 4.88
1193 | 4.96
1194 | 4.88
1195 | 4.96
1196 | 4.96
1197 | 4.88
1198 | 4.88
1199 | 5

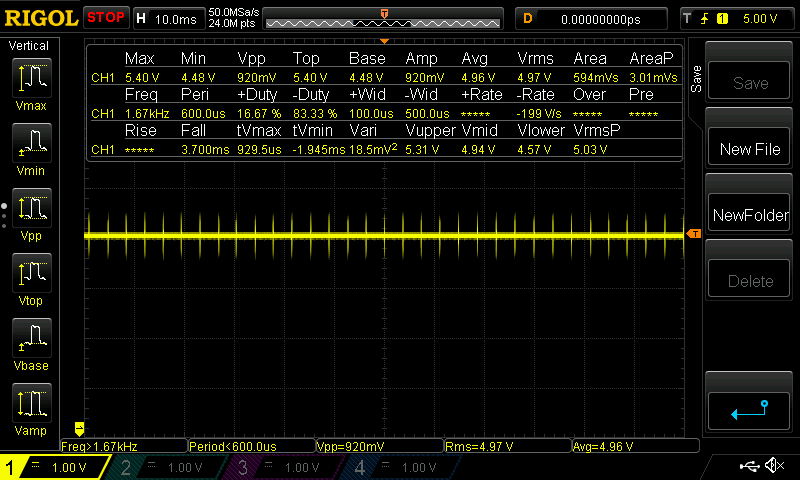
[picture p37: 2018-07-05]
Electrical/Power Supply/Testboard/Src/dcdc3.png

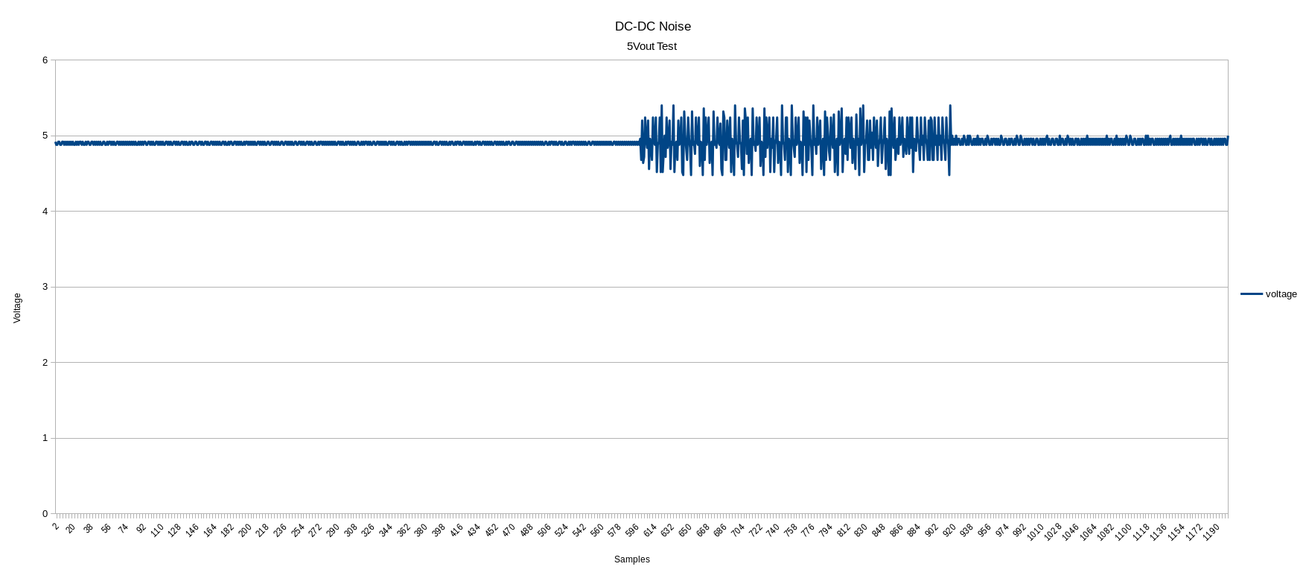
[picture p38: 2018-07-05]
Electrical/Power Supply/Testboard/DCDC-noise-plot.png

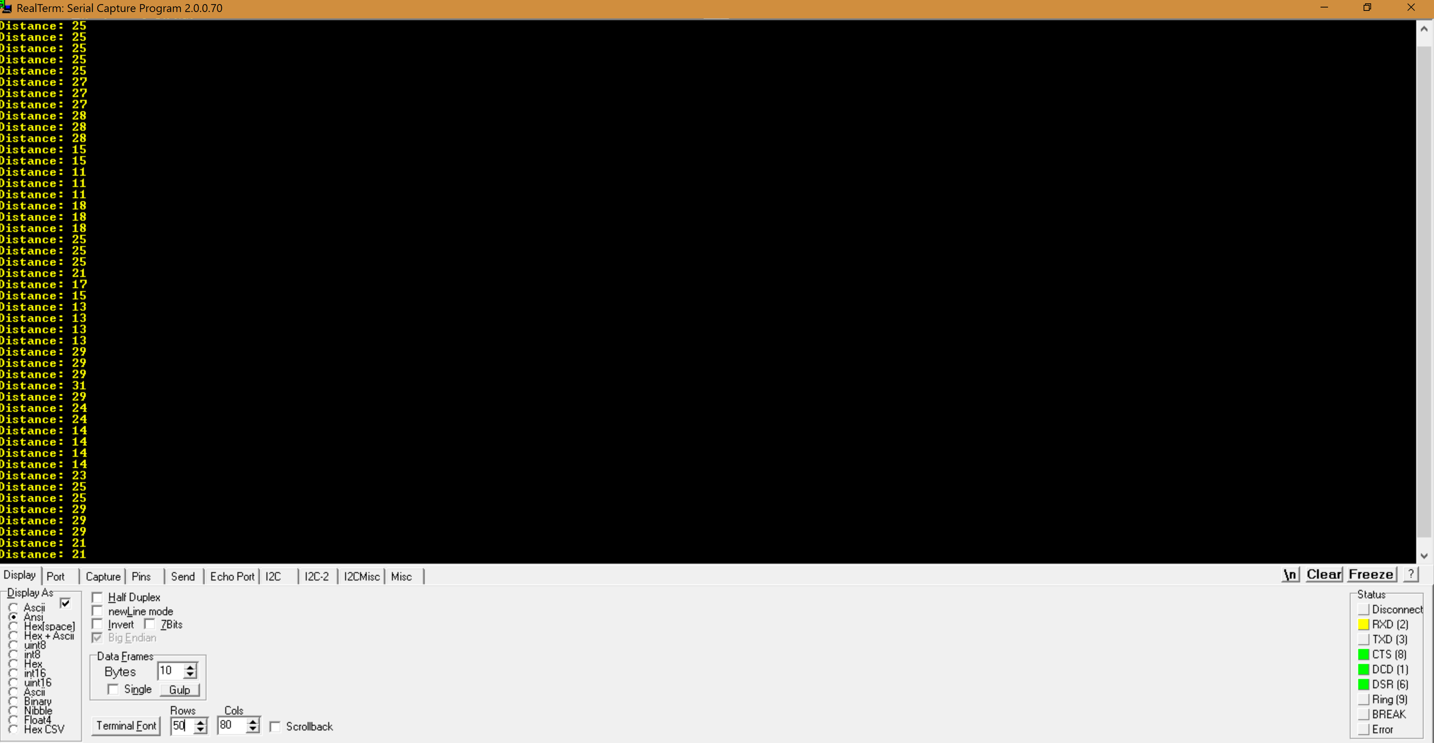
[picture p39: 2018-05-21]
Electrical/2D Assembly/Verification Screenshots/Moving.png

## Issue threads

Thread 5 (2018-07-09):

Ref Designators need matching

LinuxGogley, 2018-07-09:
Match Ref Des of CircuitMaker to OrCAD for post board fab.

LinuxGogley, 2018-07-16:
Reference designators matched per Robert & Liam's inspection.

Closed 2018-07-16.

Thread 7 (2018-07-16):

PCB Layout Drawing

LinuxGogley, 2018-07-16:
PCB drawing needs uploading to Power Supply directory

LinuxGogley, 2018-07-17:
Layout and assembly drawings added

Closed 2018-07-17.

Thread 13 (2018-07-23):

Battery selection

LinuxGogley, 2018-07-23:
Final battery choice and datasheets need to be declared.

LinuxGogley, 2018-07-30:
Powersonic 8-10Ah Deep Cycle SLA.  Order close to project due date to prevent battery depletion.

Closed 2018-07-30.

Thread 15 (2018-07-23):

Test procedure for power supply

LinuxGogley, 2018-07-23:
Write test procedure for PSU PCB, include:
- Copper test
- Temperature test
- Minimum current performance

LinuxGogley, 2018-07-24:
Attach Excel form for trace and via calculations.

LinuxGogley, 2018-08-31:
Test procedure is to verify voltages to 5% accuracy, PCB requirements have ensured current capability.

Closed 2018-08-31.

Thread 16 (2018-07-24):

PCB Rev D

LinuxGogley, 2018-07-24:
- Wider return to ground from max current
- Remove via from router 12v, and tap the source
- Remove thermal connection from polygon and vias from polygons

LinuxGogley, 2018-07-30:
Rev D submitted to boardhouse

Closed 2018-07-30.

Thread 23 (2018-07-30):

Final assembly of PCB

LinuxGogley, 2018-07-30:
Populate power supply PCB for testing.

LinuxGogley, 2018-08-31:
Estimated completion by end of September, board in production.

Closed 2018-09-18.

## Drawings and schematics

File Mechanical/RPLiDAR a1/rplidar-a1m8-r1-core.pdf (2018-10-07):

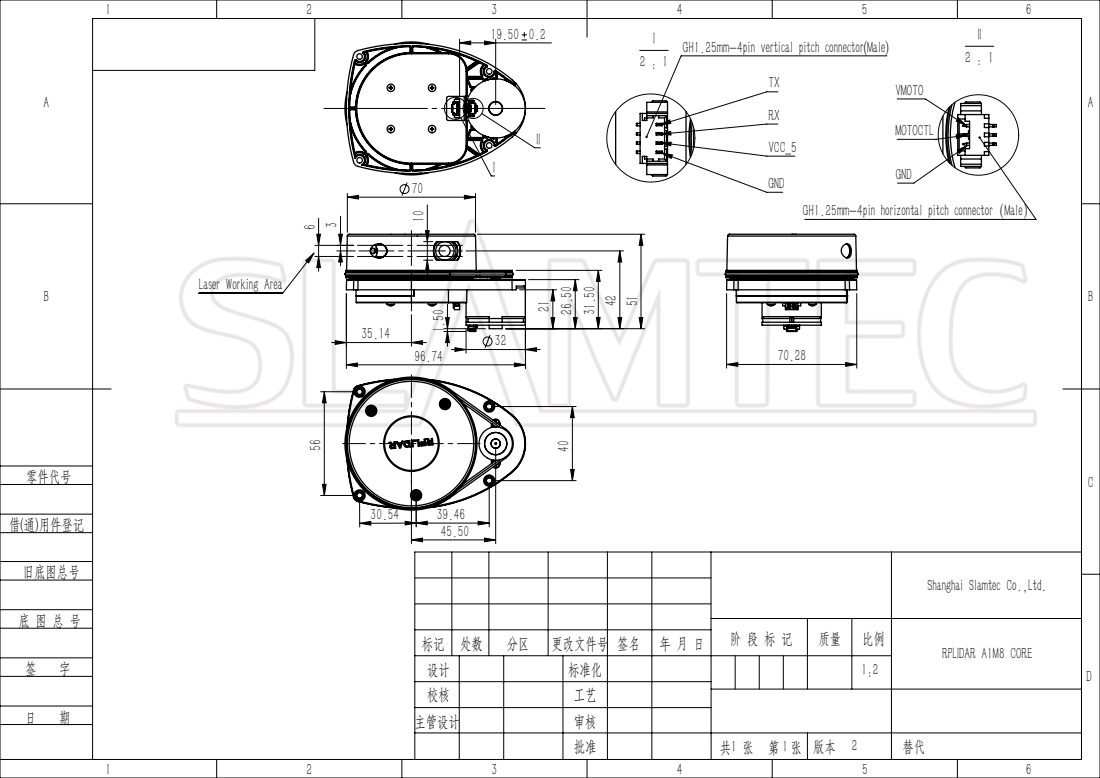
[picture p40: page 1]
GH1.25mm-4pin vertical pitch connector(Male)

GND
GH1.25mm-4pin horizontal pitch connector（Male）

Laser Working Area

Shanghai Slamtec Co.,Ltd.

阶 段 标 记 | 质量 | 比例 | RPLIDAR A1M8 CORE

标记 | 处数 | 分区 | 更改文件号 | 签名 | 年 月 日

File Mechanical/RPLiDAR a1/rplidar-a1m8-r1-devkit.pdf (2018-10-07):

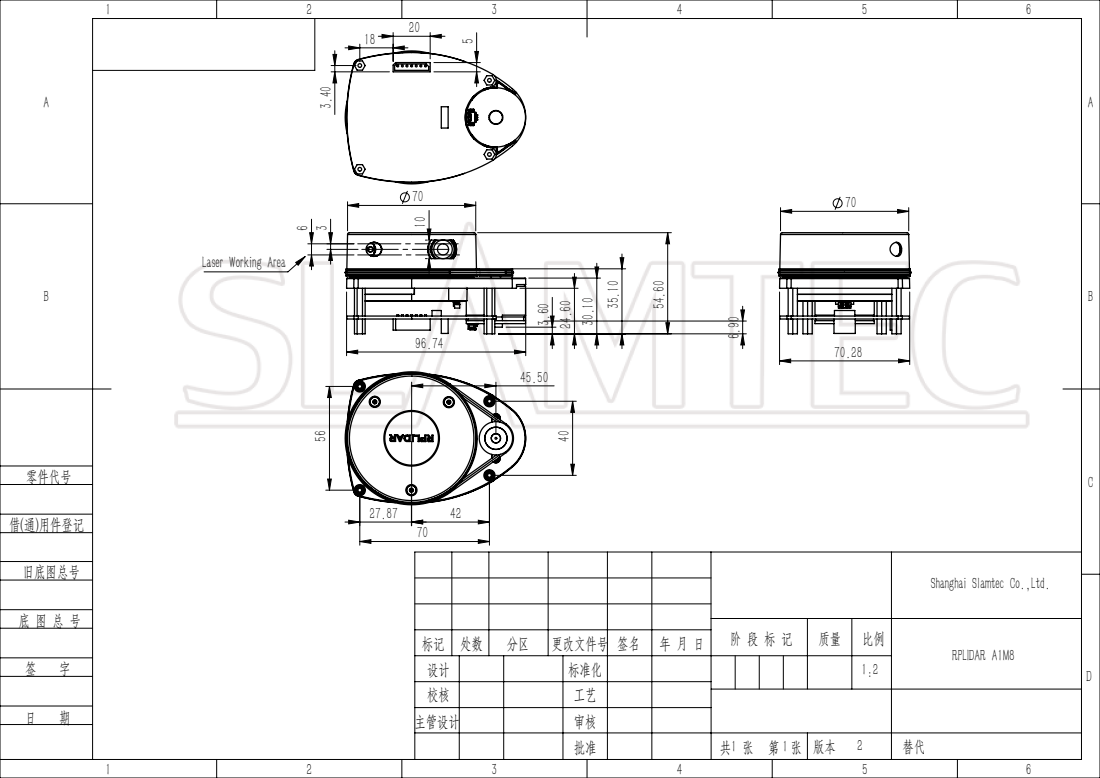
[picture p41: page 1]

Laser Working Area

Shanghai Slamtec Co.,Ltd.

阶 段 标 记 | 质量 | 比例 | RPLIDAR A1M8

标记 | 处数 | 分区 | 更改文件号 | 签名 | 年 月 日

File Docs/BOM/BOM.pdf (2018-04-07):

# 3D ROMAP

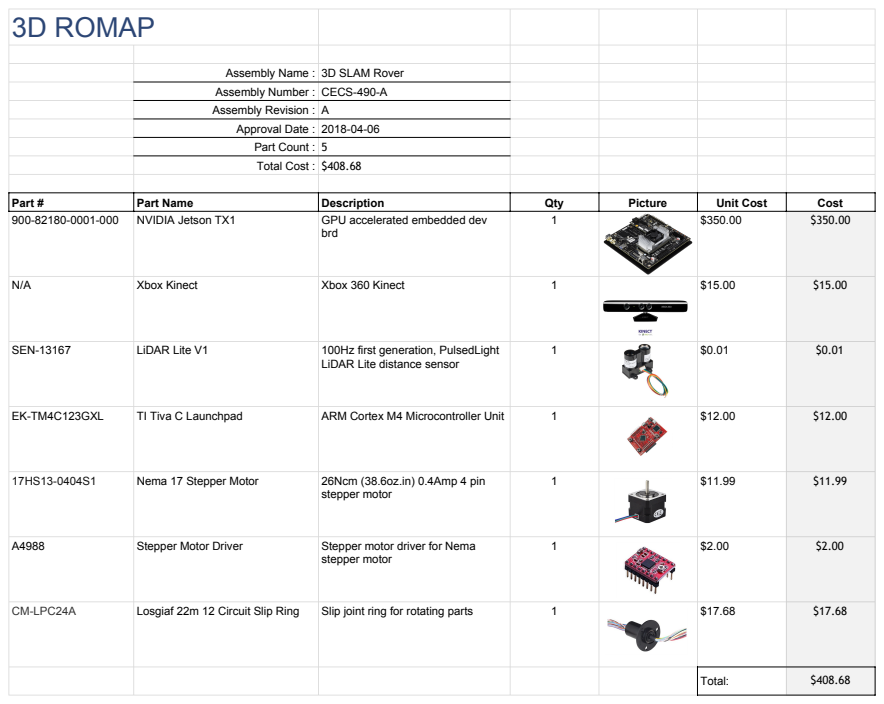
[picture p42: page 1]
Part #; Part Name; Description; Qty; Picture; Unit Cost; Cost; NVIDIA Jetson TX1; GPU accelerated embedded dev; brd; Xbox Kinect; Xbox 360 Kinect; SEN-13167; LiDAR Lite V1; 100Hz first generation, PulsedLight; EK-TM4C123GXL; TI Tiva C Launchpad; ARM Cortex M4 Microcontroller Unit; Nema 17 Stepper Motor; 26Ncm (38.6oz.in) 0.4Amp 4 pin; stepper motor; Stepper Motor Driver; Stepper motor driver for Nema; CM-LPC24A; Losgiaf 22m 12 Circuit Slip Ring; Slip joint ring for rotating parts; Total:

Assembly Name : 3D SLAM Rover
Assembly Number : CECS-490-A
Assembly Revision : A
Approval Date : 2018-04-06
Part Count : 5
Total Cost : $408.68

LiDAR Lite distance sensor

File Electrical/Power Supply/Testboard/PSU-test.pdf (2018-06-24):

# CAL STATE LONG BEACH - COMPUTER ENGINEERING

# 3D-ROBOTIC MAPPING PLATFORM

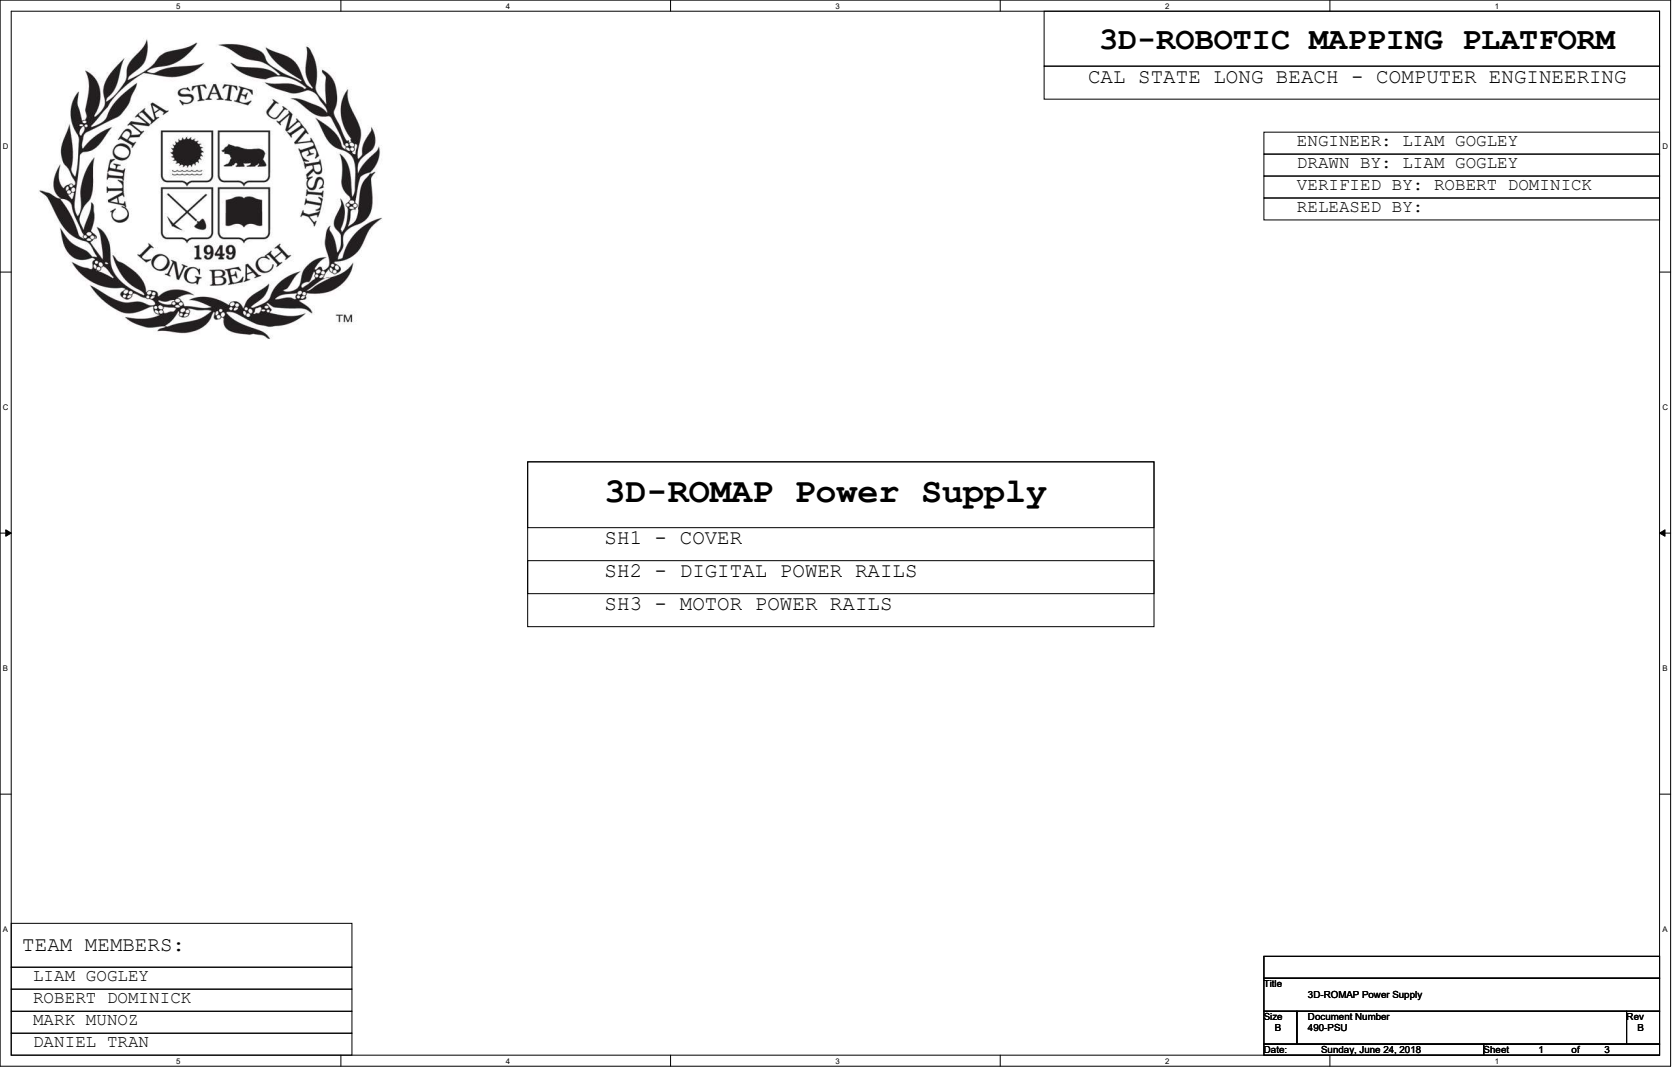
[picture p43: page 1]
A A TEAM MEMBERS:; ROBERT DOMINICK; LIAM GOGLEY; MARK MUNOZ DANIEL TRAN; Title; Size; Document Number; Rev; Date:; Sheet; 490-PSU; Sunday, June 24, 2018

ENGINEER: LIAM GOGLEY
DRAWN BY: LIAM GOGLEY
VERIFIED BY: ROBERT DOMINICK
RELEASED BY:

3D-ROMAP Power Supply

SH1 - COVER
SH2 - DIGITAL POWER RAILS
SH3 - MOTOR POWER RAILS

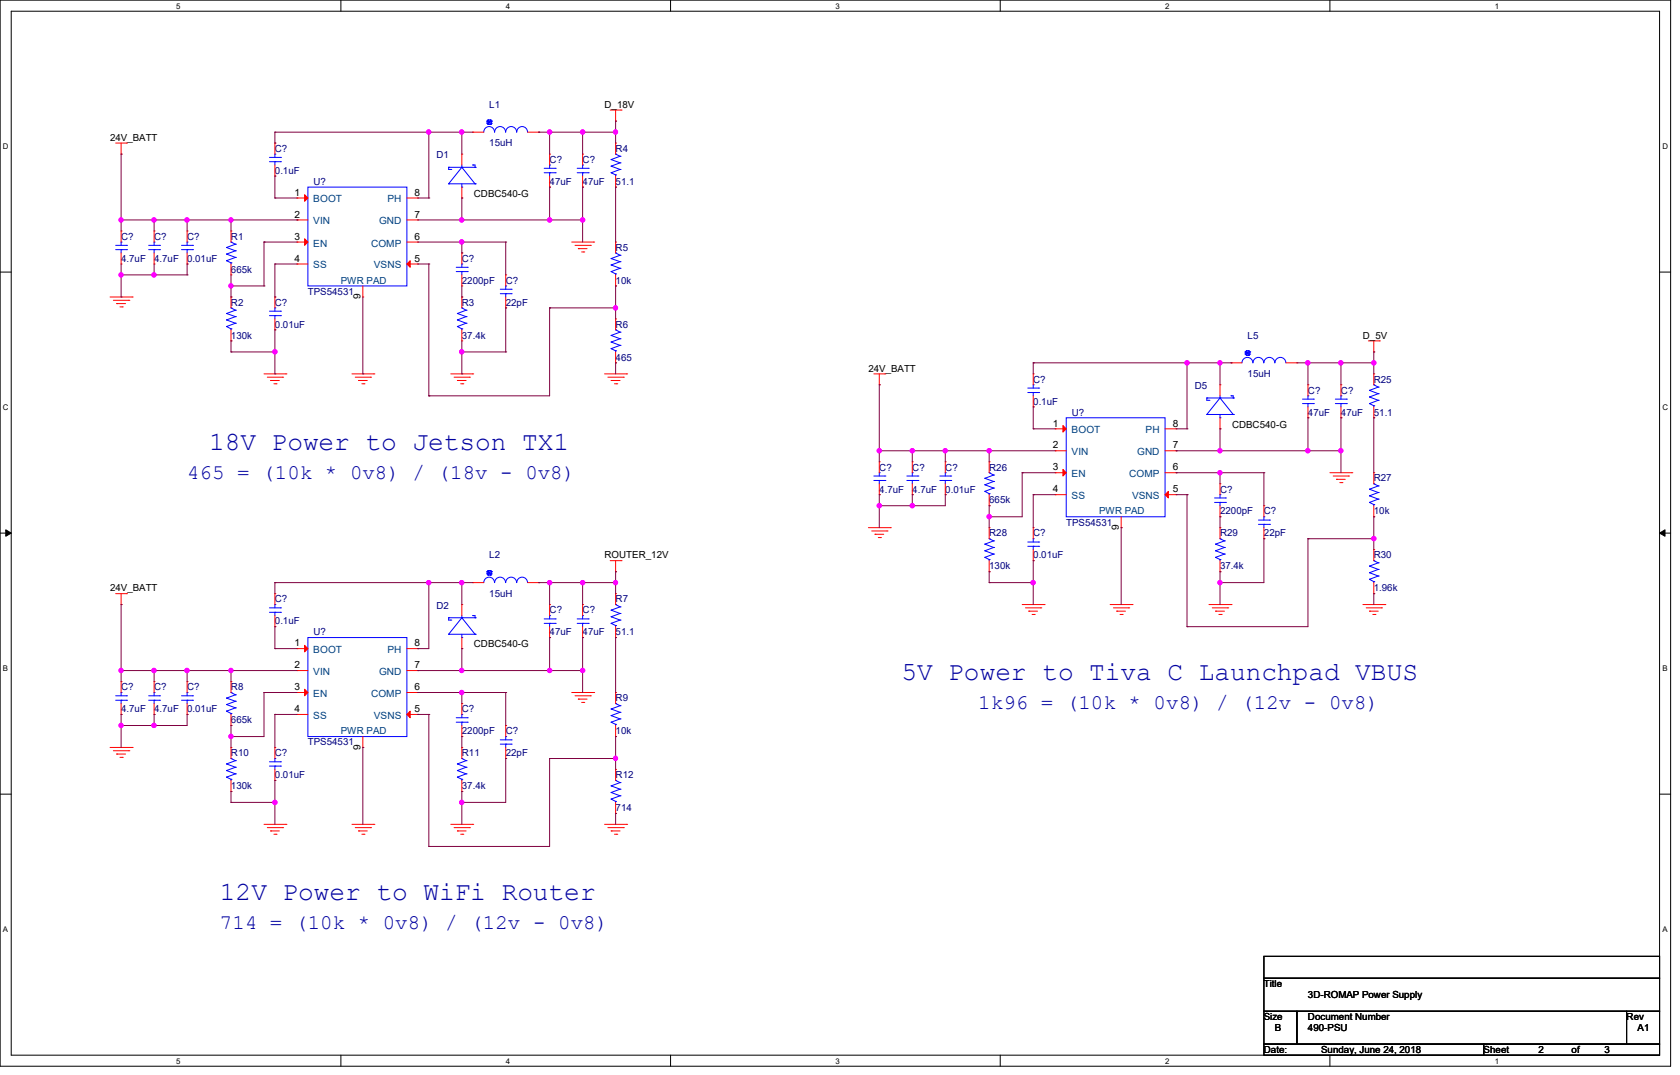
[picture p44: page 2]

5V Power to Tiva C Launchpad VBUS

12V Power to WiFi Router

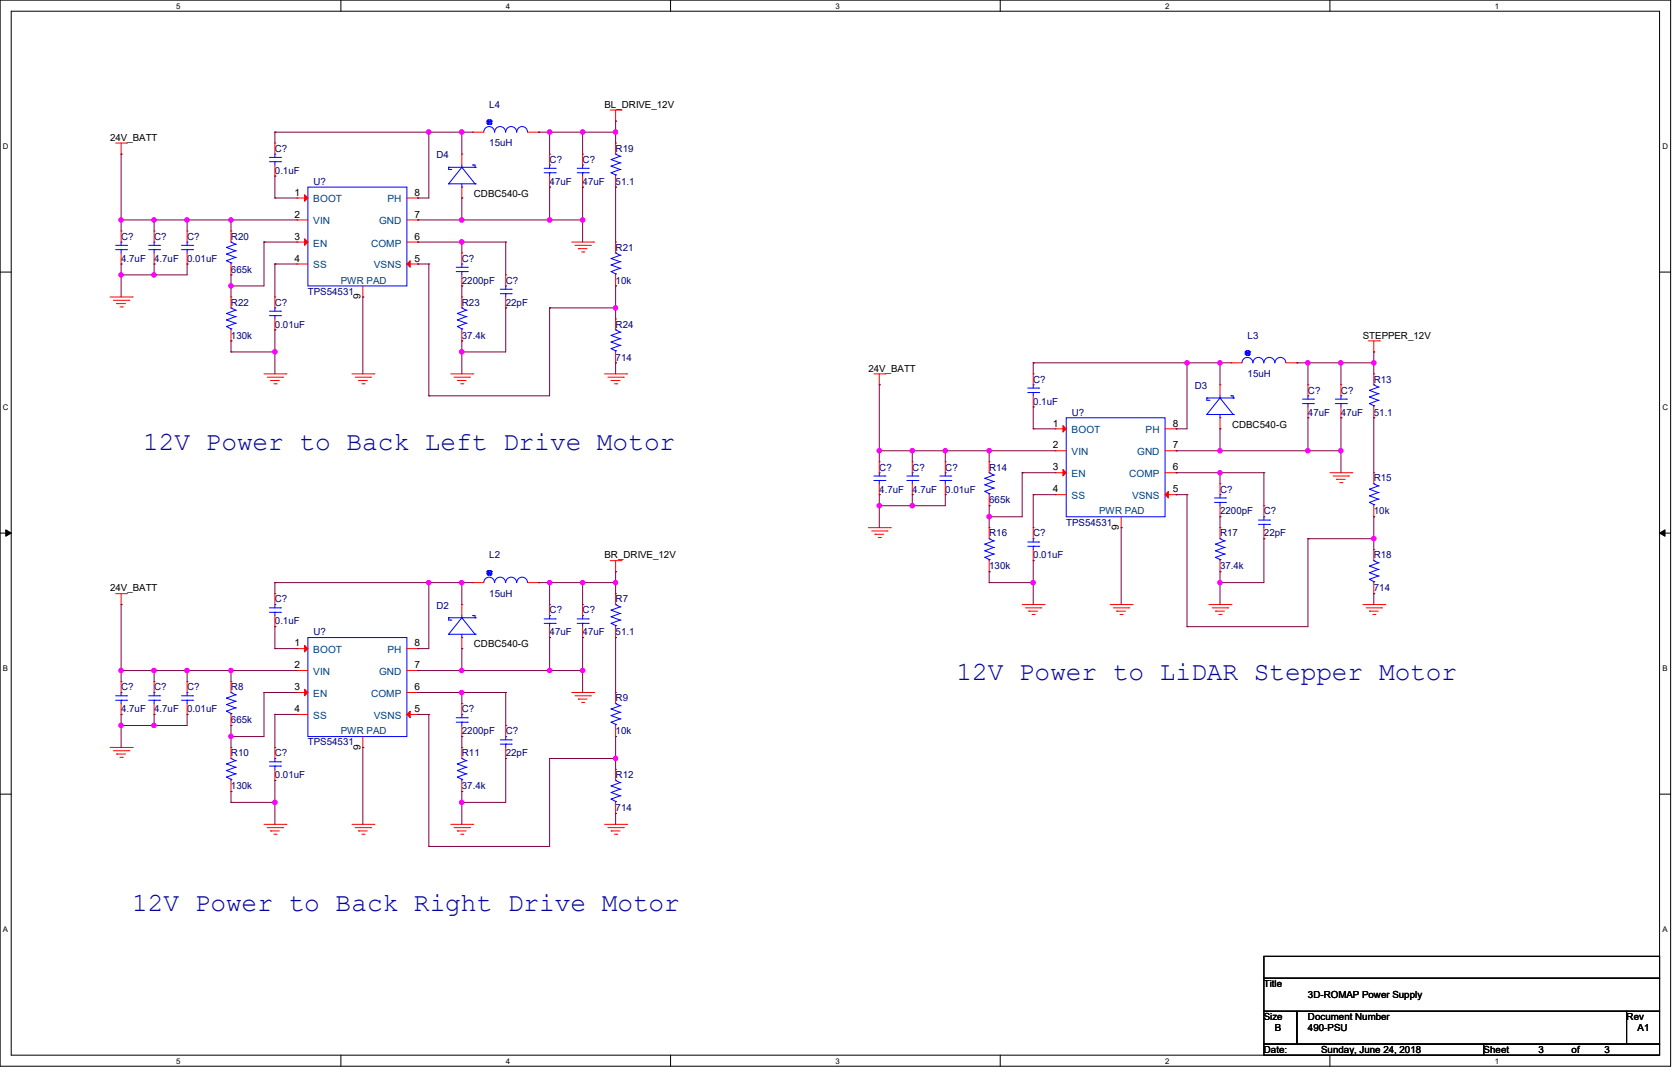
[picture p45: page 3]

12V Power to Back Left Drive Motor

12V Power to LiDAR Stepper Motor

12V Power to Back Right Drive Motor

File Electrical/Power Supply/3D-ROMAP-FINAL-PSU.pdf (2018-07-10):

# CAL STATE LONG BEACH - COMPUTER ENGINEERING

# 3D-ROBOTIC MAPPING PLATFORM

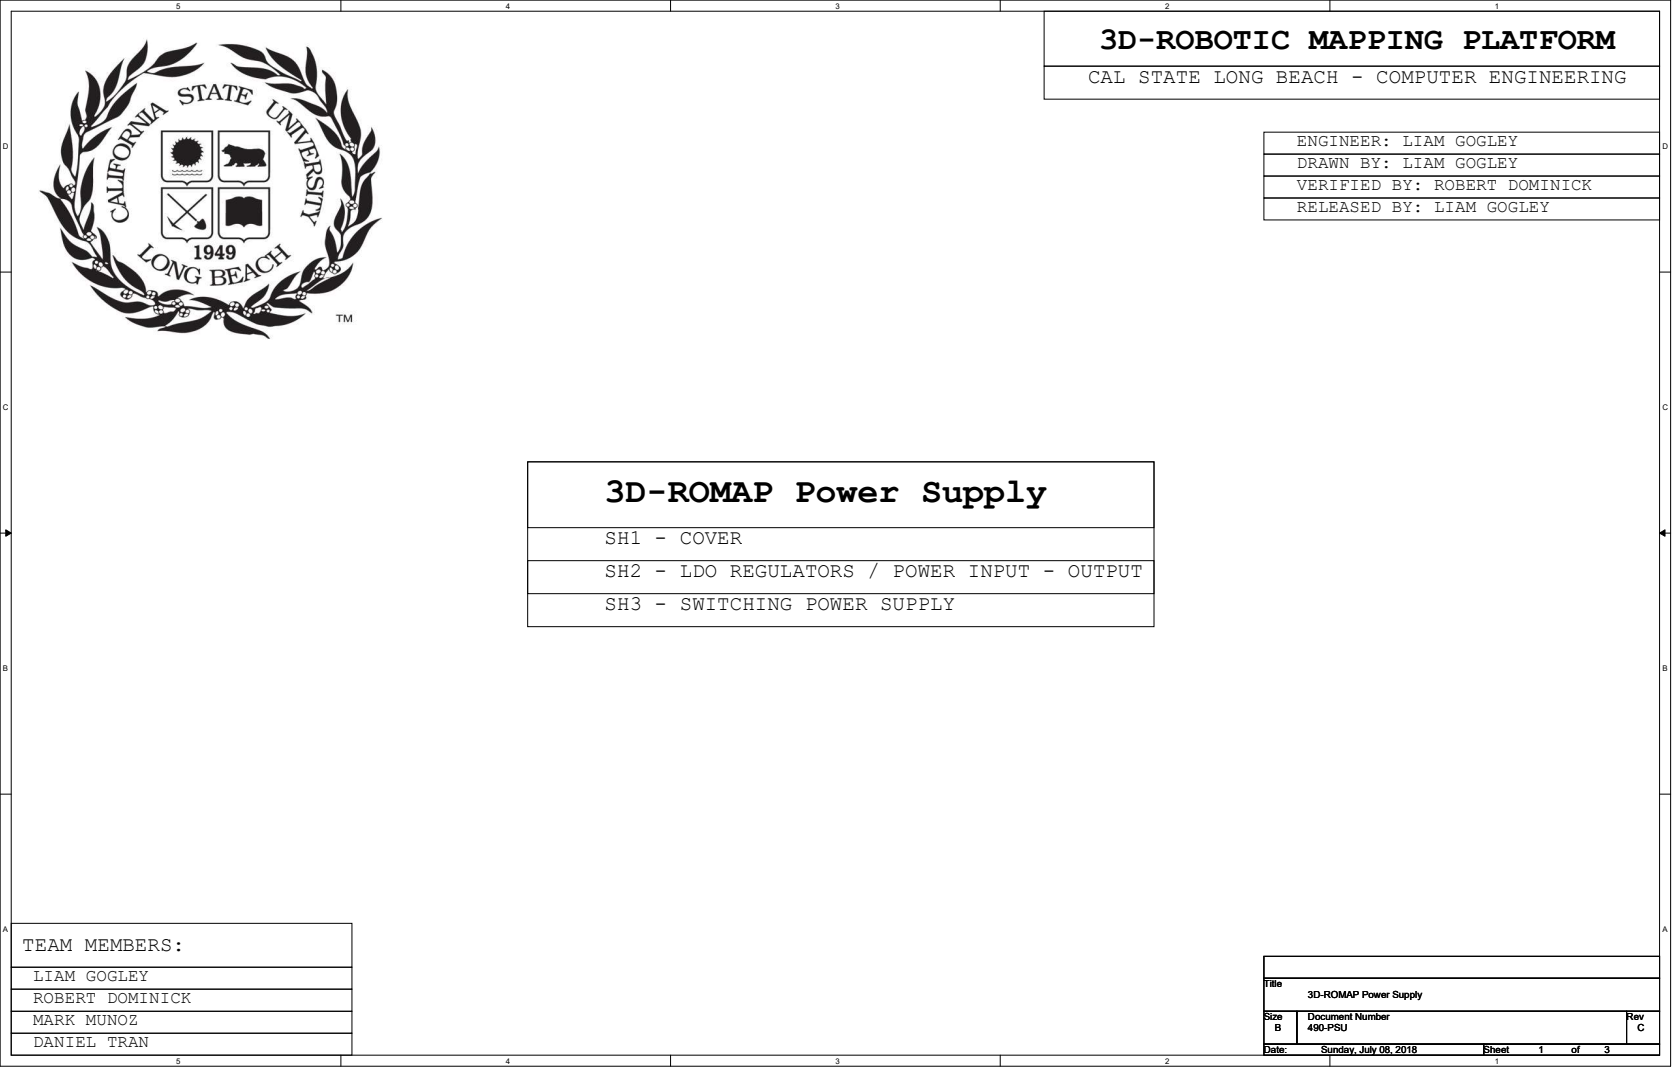
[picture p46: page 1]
A A TEAM MEMBERS:; ROBERT DOMINICK; LIAM GOGLEY; MARK MUNOZ DANIEL TRAN; Title; Size; Document Number; Rev; Date:; Sheet; 490-PSU; Sunday, July 08, 2018

ENGINEER: LIAM GOGLEY
DRAWN BY: LIAM GOGLEY
VERIFIED BY: ROBERT DOMINICK
RELEASED BY: LIAM GOGLEY

3D-ROMAP Power Supply

SH1 - COVER
SH2 - LDO REGULATORS / POWER INPUT - OUTPUT
SH3 - SWITCHING POWER SUPPLY

# INPUT PWR FROM BATTERY

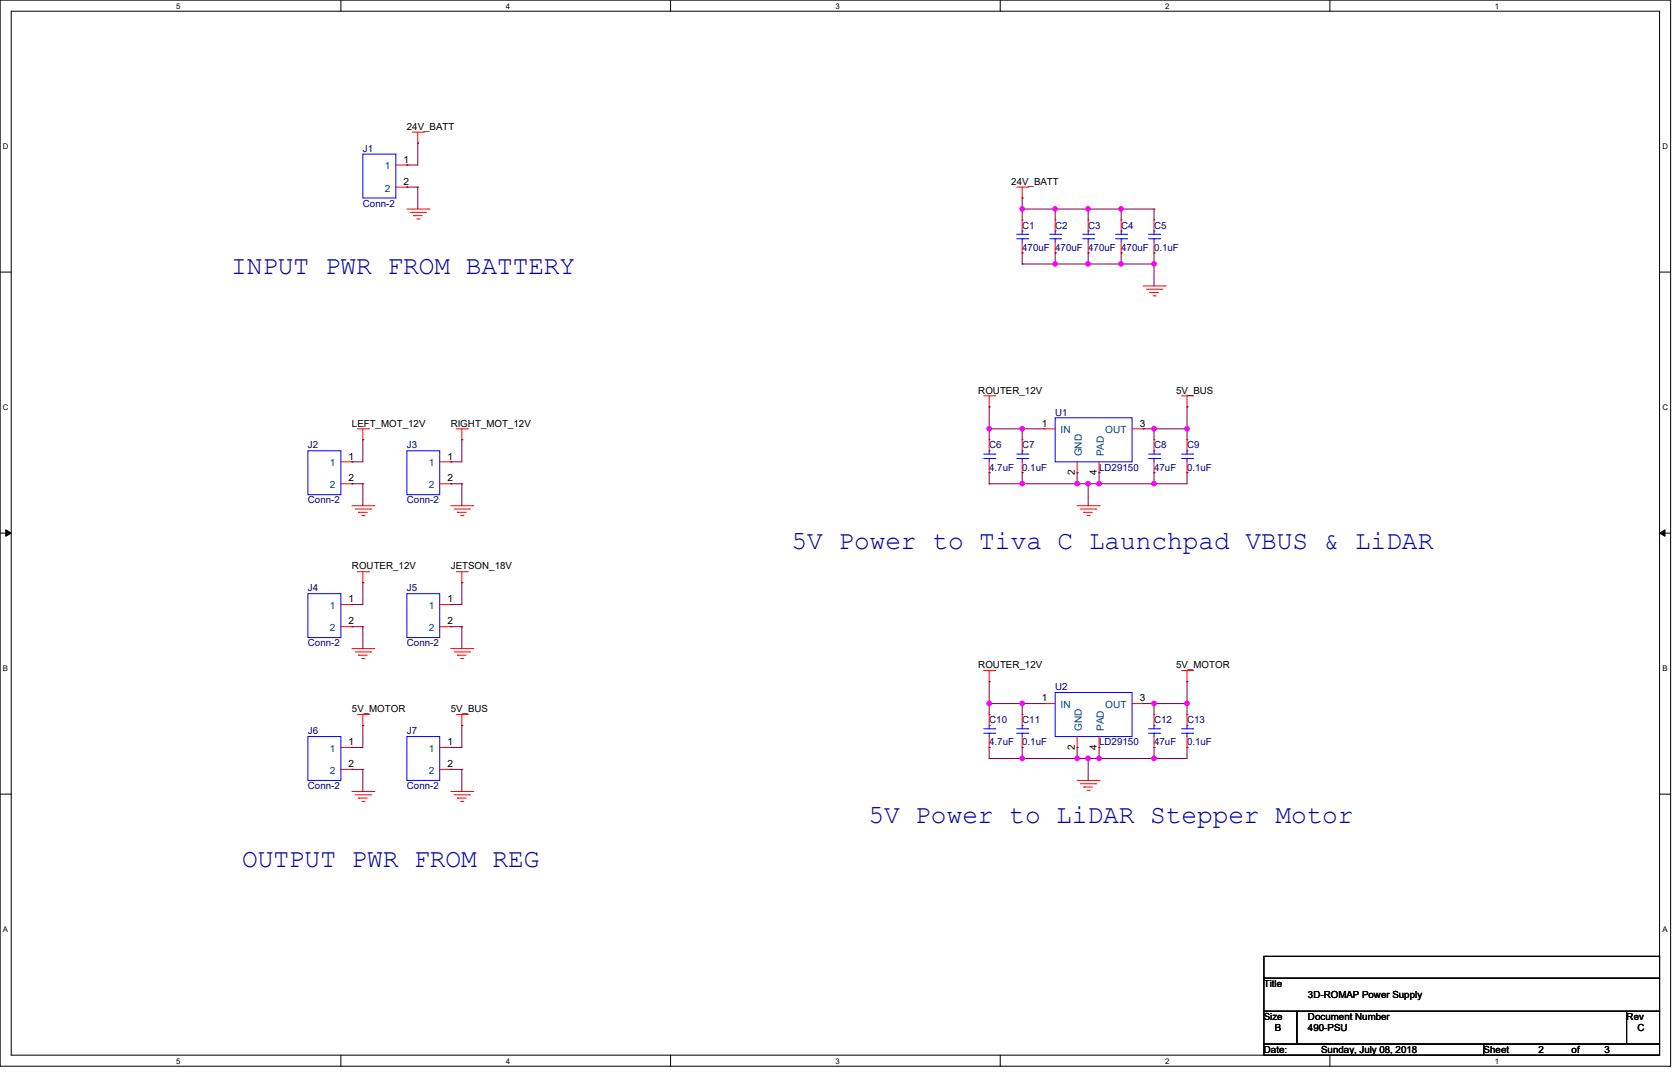
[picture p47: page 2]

5V Power to Tiva C Launchpad VBUS & LiDAR

5V Power to LiDAR Stepper Motor

OUTPUT PWR FROM REG

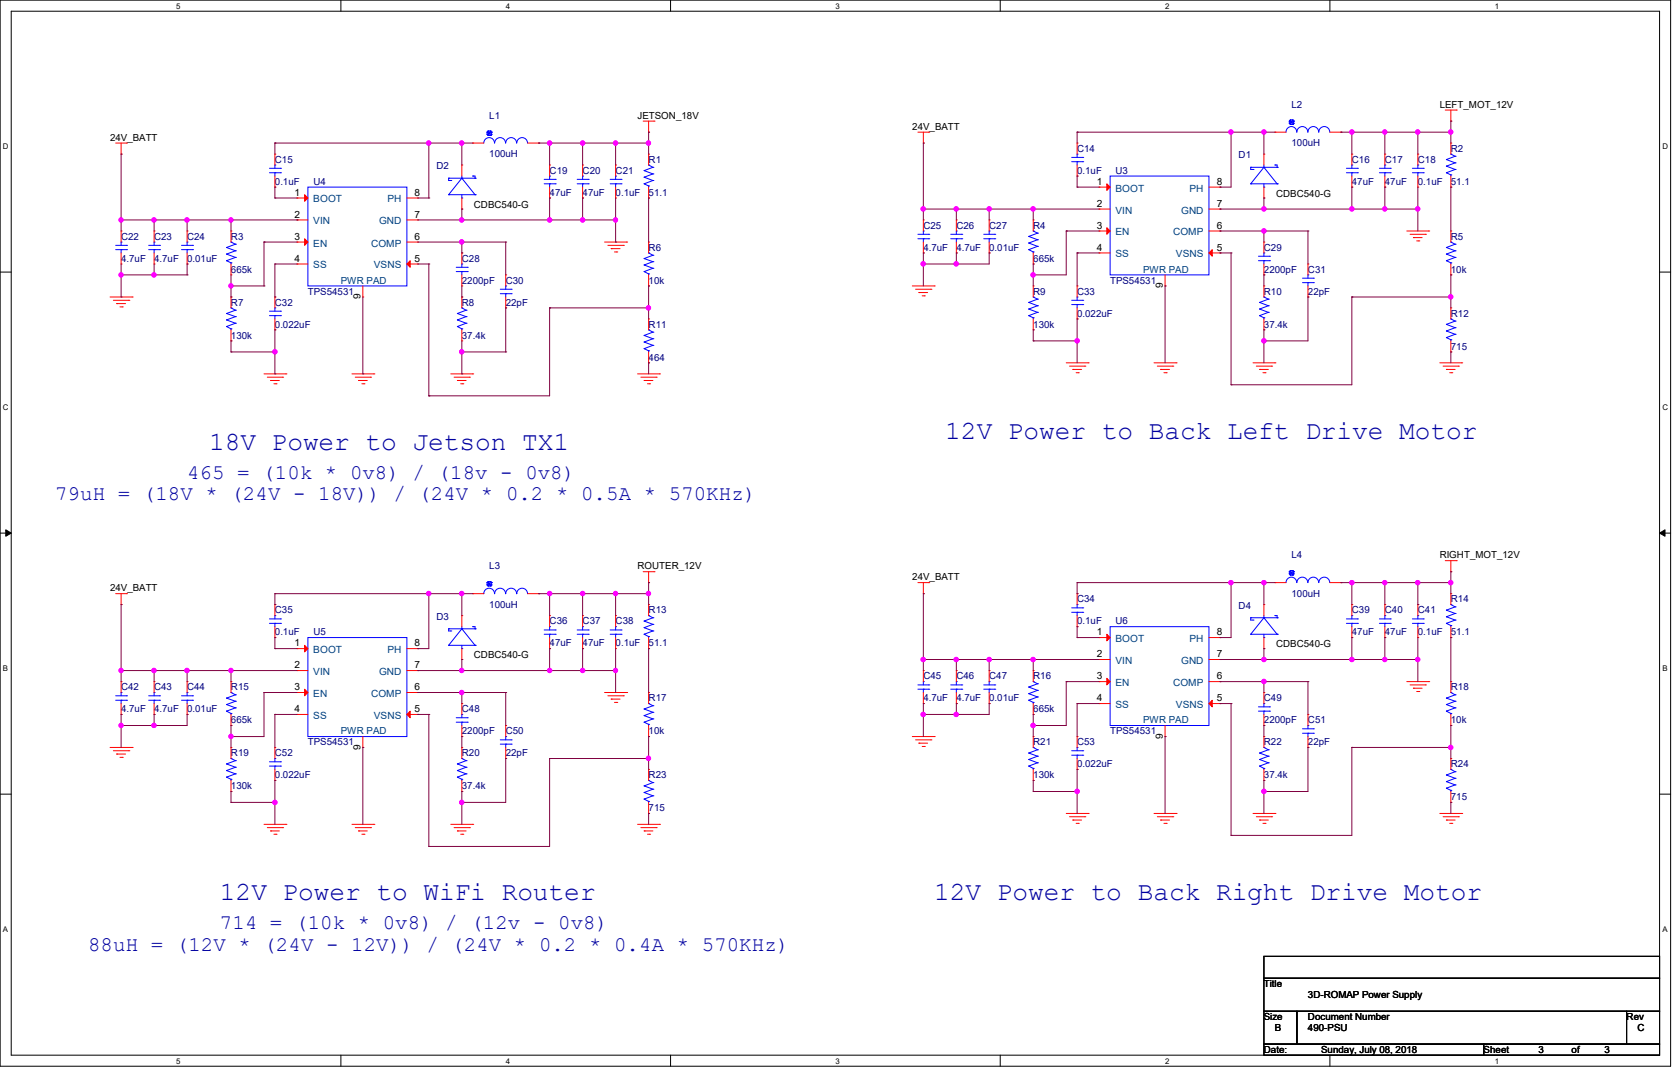
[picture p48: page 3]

12V Power to Back Left Drive Motor

12V Power to WiFi Router

12V Power to Back Right Drive Motor

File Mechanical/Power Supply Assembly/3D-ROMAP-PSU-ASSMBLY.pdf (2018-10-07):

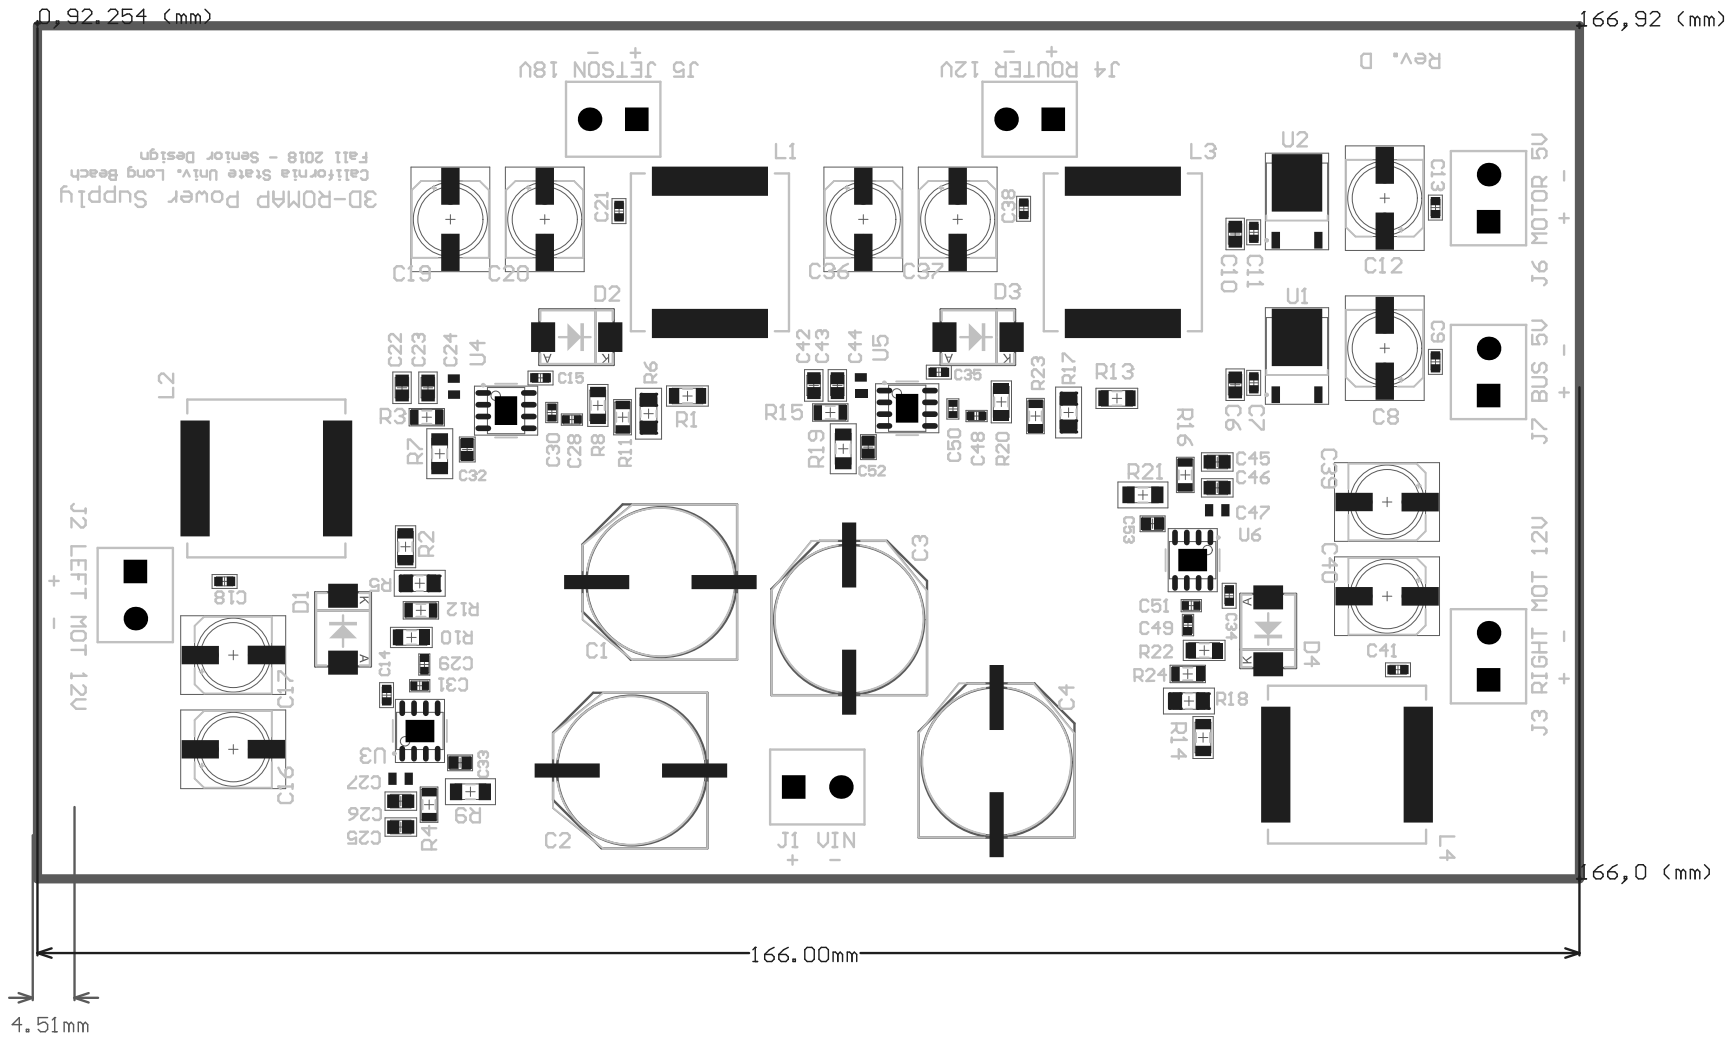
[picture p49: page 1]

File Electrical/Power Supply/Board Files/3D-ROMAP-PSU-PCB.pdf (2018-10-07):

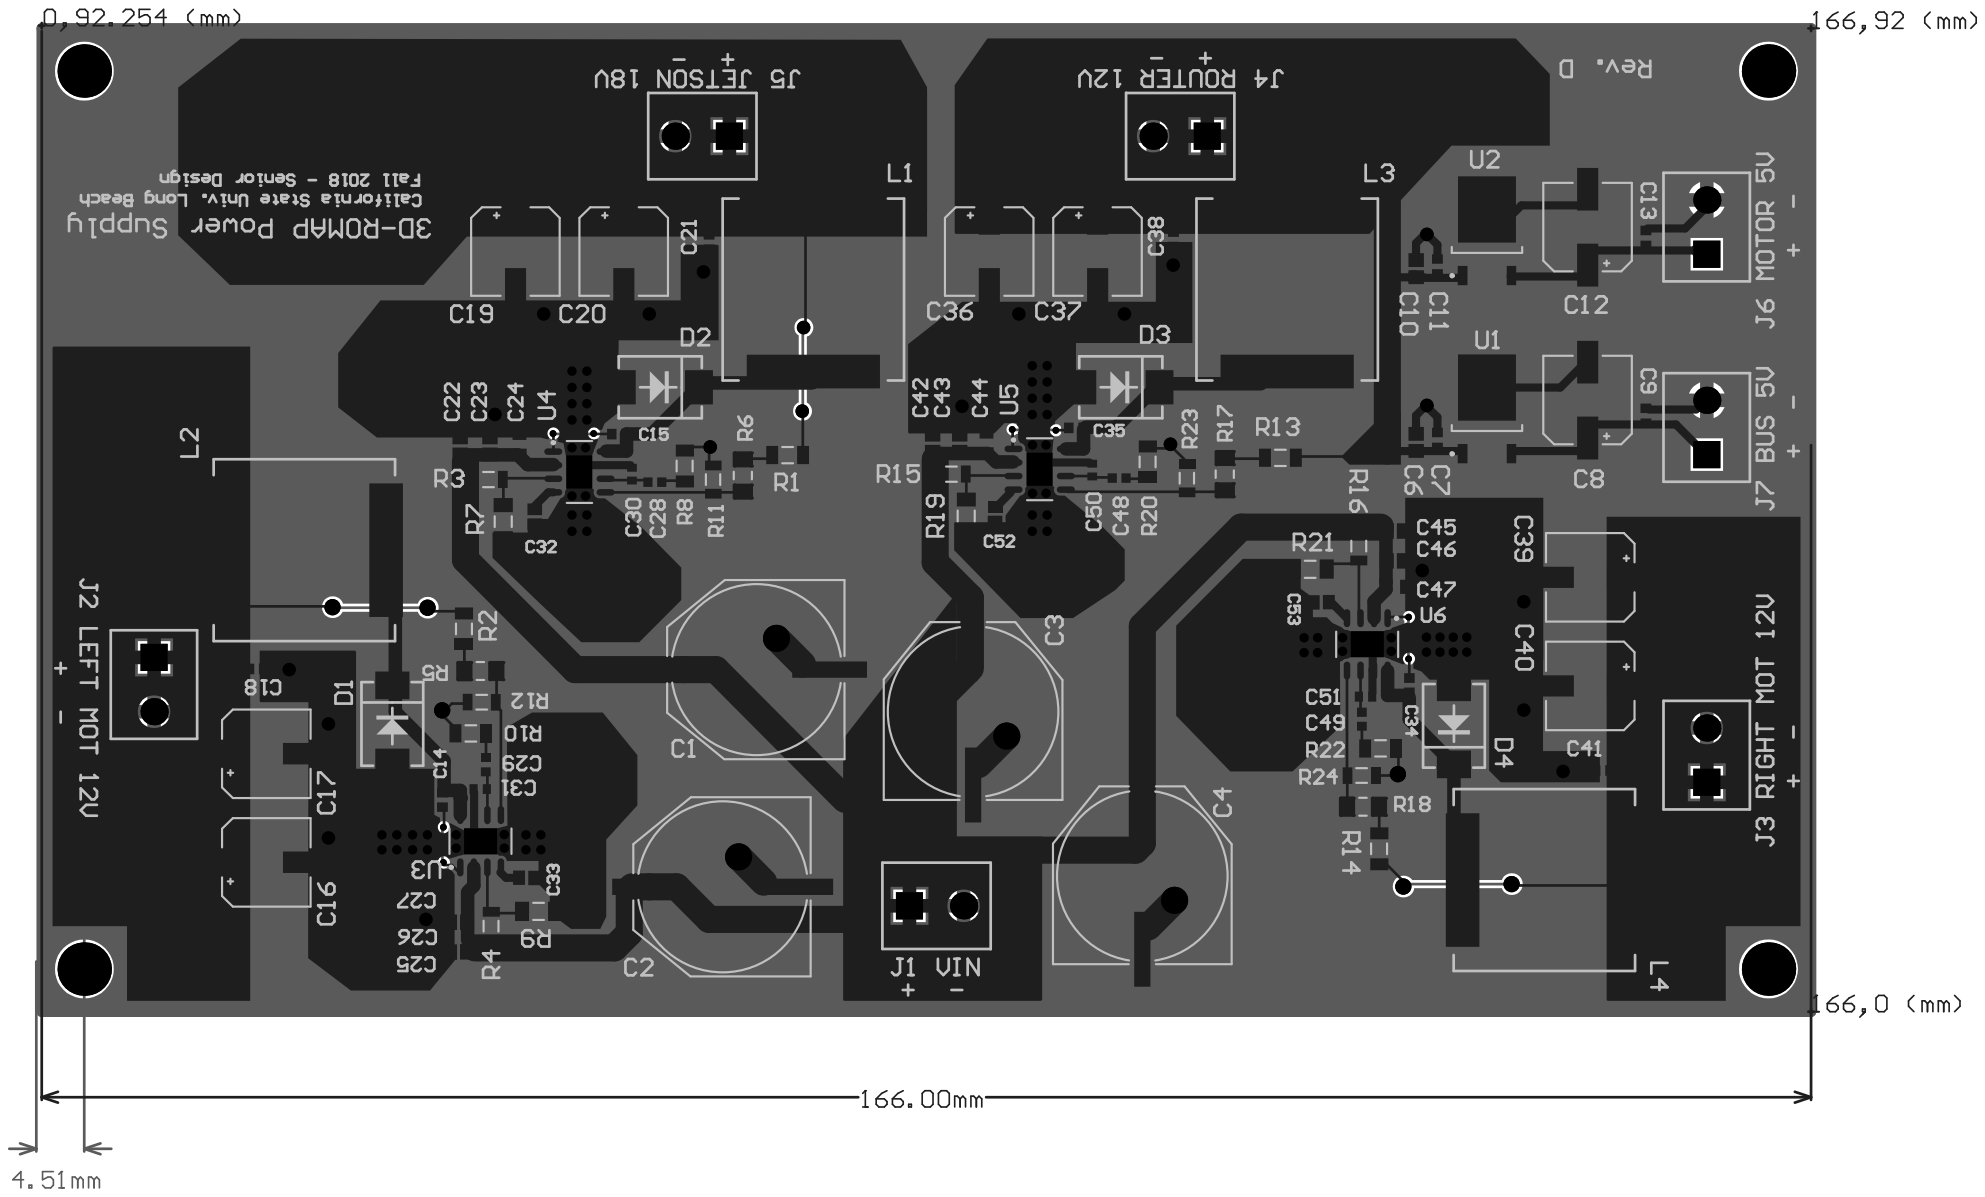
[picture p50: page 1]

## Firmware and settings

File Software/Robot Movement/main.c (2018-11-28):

/***********************************************************************;
;      File name: main.c                                                ; 
;                                                                       ;
;      Created by: Mark Munoz, Nov. 2018                                ; 
;                                                                       ; 
;      Bluetooth controlled robotic platform for 3DROMAP senior design. ;
;      Standard WASD directional movement control with 3 selectable     ;
;      speeds: 50%, 75%, or 100%. Runs on TM4C                          ;
/***********************************************************************/

// 1. Pre-processor Directives Section
// include header files that contain 
// function prototypes and constant definitions
#include "PLL.h"
#include "UART.h"
#include "PWM.h"
#include "String.h"
#include "tm4c123gh6pm.h"


// 2. Misc. Function Prototypes
void DisableInterrupts(void); // Disable interrupts
void EnableInterrupts(void);  // Enable interrupts
void PortF_Init(void);
	
	
// 3. Main loop
int main(void){
	const unsigned long period = 1000;  // (40MHz PLL clk / period / 2) = 20KHz PWM 
	unsigned long dutyA, dutyB, dutyMax;
	char mode [6];            // controls action based on bluetooth input
	PLL_Init();               // PLL w/ 40Mhz bus clk
	UART1_Init();             // HC05 UART 57600 baud, 8O1 
	PortF_Init();             
	Direction_Init();         // Init PD0 and PD1 as motor direction signals, PD2 as output enable
    GPIO_PORTD_DATA_R |= 0x04;// enables motors output
	PWM0A_Init(period, 3); 
	PWM0B_Init(period, 3);    
	dutyMax = period/2;       

	//**************Configure bluetooth Commands*************
	//UART1_OutString("AT+NAME=3D-ROMAP\r\n");    
    //UART1_OutString("AT+PSWD=0159\r\n");         
	//UART1_OutString("AT+UART=57600,0,1\r\n");    // 57600 baud, 8O1

	while(1){
		UART1_InString(mode);           // receive updated mode from bluetooth
		
		if(strncmp(mode, "w", 1) == 0){  
			GPIO_PORTF_DATA_R |=  0x02; // RED LED
			GPIO_PORTD_DATA_R &= ~0x03; // ensure motors going forward
			dutyA = dutyB = dutyMax;    
		}
		
		else if(strncmp(mode, "a", 1) == 0){  
			GPIO_PORTF_DATA_R |= 0x04;  // BLUE LED
			GPIO_PORTD_DATA_R |= 0x02;  // motor A reverse
			GPIO_PORTD_DATA_R &=~0x01;  // motor B forward
			dutyA = dutyB = dutyMax;    
		}
		
		else if(strncmp(mode, "s", 1) == 0){    
			GPIO_PORTF_DATA_R |= 0x08;  // GEEN LED
			GPIO_PORTD_DATA_R |= 0x03;  // both motors reverse
			dutyA = dutyB = dutyMax;    
		}
		
		else if(strncmp(mode, "d", 1) == 0){  
			GPIO_PORTF_DATA_R |= 0x0E;  // WHITE LED
			GPIO_PORTD_DATA_R |= 0x01;  // motor B reverse
			GPIO_PORTD_DATA_R &=~0x02;  // motor A forward
			dutyA = dutyB = dutyMax;    
		}
		
		else if(strncmp(mode, "50%", 1) == 0){
			GPIO_PORTF_DATA_R |= 0x0A;  // debug LED
			dutyMax = .5*period;        // 50% max speed
		}
		
		else if(strncmp(mode, "75%", 1) == 0){
			GPIO_PORTF_DATA_R |= 0x0C;  // YELLOW LED
			dutyMax = .75*period;       // 75% max speed
		}
		
		else if(strncmp(mode, "100%", 1) == 0){
			GPIO_PORTF_DATA_R |= 0x02;  // RED LED
			dutyMax = period - 2;       // 100% max speed
		}
		else if(strncmp(mode, "q", 1) == 0){ 
			GPIO_PORTF_DATA_R &= ~0x0E; // clear debug LEDs
			GPIO_PORTD_DATA_R &= ~0x03; // set both motors forward 
			dutyA = dutyB = 3;          // set pwm to 0
		}
		PWM0A_Duty(dutyA*(2/3.0));      // update motor PWMs
		PWM0B_Duty(dutyB*(2/3.0));      // run at max 12v (2/3 of 18v source)		
	}
}

// 4. Subroutines Section
// Init PortF for debug LEDs
void PortF_Init(void){ 
  volatile unsigned long delay;     // dummy instruction variable
  SYSCTL_RCGC2_R |= 0x00000020;     // 1) F clock
  delay = SYSCTL_RCGC2_R;           // dummy instruction to give setup enough time   
  GPIO_PORTF_LOCK_R  |=  0x4C4F434B;// 2) unlock PortF PF0  
  GPIO_PORTF_CR_R    |=  0x0E;      // allow changes to PF4-PF1     
  GPIO_PORTF_AMSEL_R &= ~0x0E;      // 3) disable analog function
  GPIO_PORTF_PCTL_R  &= ~0x0000FFF0;// 4) GPIO clear bit PCTL  
  GPIO_PORTF_DIR_R   |=  0x0E;      //    PF3-PF1 is output
  GPIO_PORTF_AFSEL_R &= ~0x0E;      // 6) no alternate function on PF4-PF1
  GPIO_PORTF_PUR_R   &= ~0x0E;      //    disable pullup resistors for LED
  GPIO_PORTF_DEN_R   |=  0x0E;      // 7) enable digital pins PF4-PF1 
  }

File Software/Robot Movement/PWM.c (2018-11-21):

// PWM.c
// Initializes hardware PWM to control motors
//
#include "PWM.h"
#include "tm4c123gh6pm.h"

	// Output on PB4/M0PWM0
void PWM0A_Init(unsigned long period, unsigned long duty){
	// Initializing PWM on PB4/M0PWM2
	SYSCTL_RCGCPWM_R |= 0x01;		// 1) Activate PWM0
	SYSCTL_RCGCGPIO_R |= 0x02;	// 2) Activate Port B
	while((SYSCTL_PRGPIO_R&0x02) == 0){};
	GPIO_PORTB_AFSEL_R |= 0x10;    // Enable Alt Funct on PB4 
	GPIO_PORTB_PCTL_R &= ~0x000F0000; // Configure PB4 as PWM0
	GPIO_PORTB_PCTL_R |=  0x00040000;
	GPIO_PORTB_AMSEL_R &= ~0x10;  // Disable analog function on PB4
	GPIO_PORTB_DEN_R |= 0x10;     // Enable digital I/O on PB4
	SYSCTL_RCC_R = 0x00100000 |   // 3) use PWM divider
			(SYSCTL_RCC_R & (~0x000E0000));   // configure for /2 divider
	PWM0_1_CTL_R = 0;             // 4) Reload down-count mode
	PWM0_1_GENA_R = 0xC8;					// Low on LOAD, high on CMPA down
	PWM0_1_LOAD_R = period - 1;   // 5) Cycles needed to count down to 0
	PWM0_1_CMPA_R = duty - 1;			// 6) Count value when output rises
	PWM0_1_CTL_R  |= 0x00000001;
	PWM0_ENABLE_R |= 0x00000004;		 // Enable PB4 - PWM2EN (Pg.1247)
}

// Output on PB5/M0PWM3
void PWM0B_Init(unsigned long period, unsigned long duty){
	volatile unsigned long delay;
	// Initializing PWM on PB5/M0PWM2
	SYSCTL_RCGCPWM_R |= 0x01;		// 1) Activate PWM0
	SYSCTL_RCGCGPIO_R |= 0x02;	// 2) Activate Port B
	delay = SYSCTL_RCGCGPIO_R;            // allow time to finish activating
	GPIO_PORTB_AFSEL_R |= 0x20;    // Enable Alt Funct on PB5 (0010 0000)
	GPIO_PORTB_PCTL_R &= ~0x00F00000; // Configure PB5 as PWM0
	GPIO_PORTB_PCTL_R |=  0x00400000;	// Pin Mux(4)	
	GPIO_PORTB_AMSEL_R &= ~0x20;  // Disable analog function on PB5
	GPIO_PORTB_DEN_R |= 0x20;     // Enable digital I/O on PB5
	SYSCTL_RCC_R |= SYSCTL_RCC_USEPWMDIV; // 3) use PWM divider
	SYSCTL_RCC_R &= ~SYSCTL_RCC_PWMDIV_M; //    clear PWM divider field
	SYSCTL_RCC_R += SYSCTL_RCC_PWMDIV_2;  //    configure for /2 divider
	PWM0_1_CTL_R = 0;             // 4) Reload down-count mode
	PWM0_1_GENB_R = (PWM_0_GENB_ACTCMPBD_ONE|PWM_0_GENB_ACTLOAD_ZERO);
	PWM0_1_LOAD_R = period - 1;   // 5) Cycles needed to count down to 0
	PWM0_1_CMPB_R = duty - 1;			// 6) Count value when output rises		
	PWM0_1_CTL_R  |= 0x00000001;   //7) start PWM0
	PWM0_ENABLE_R |= 0x00000008;   // enable PB5/M0PWM0
}

// change duty cycle of PB4
// duty is number of PWM clock cycles output is high  (2<=duty<=period-1)
void PWM0A_Duty(unsigned long duty){
	PWM0_1_CMPA_R = duty - 1;             // 6) count value when output rises
}


// change duty cycle of PB5
// duty is number of PWM clock cycles output is high 
void PWM0B_Duty(unsigned long duty){
	PWM0_1_CMPB_R = duty - 1;             // 6) count value when output rises
}

// Initialize PD0 and PD1 as motor direction signals	
// and PD2 as motor output enable
void Direction_Init(void) {
	// Port D Initialization
	SYSCTL_RCGC2_R     |=  0x08;       // Enable port D clock
  GPIO_PORTD_CR_R 	 |=  0x07;       // Enable changes to PD2-PD0
  GPIO_PORTD_AMSEL_R &= ~0x07;       // Disable analog PD2-PD0 
  GPIO_PORTD_PCTL_R  &= ~0x00000FFF; // Configure PD2-PD0 as GPIO 
  GPIO_PORTD_DIR_R 	 |=  0x07;       // Set PD2-PD0 as output
  GPIO_PORTD_AFSEL_R &= ~0x07;       // Disable alternate functionality  
  GPIO_PORTD_DEN_R 	 |=  0x07;       // Digital enable PD2-PD0
}

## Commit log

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2018-06-14 RS Frame Capture Testing
    Pointcloud generated in .PLY formatting using RS-Frame_Capture.cpp
    [Captured_Frame.ply]
2018-06-15 Revert "Edit"
    This reverts commit e3b076ecaaed761a259e0e1c17d8ba8416d7ad4d.
    new file: Engineering/Software/PCL-Realsense-Capture/RS_Testing/Captured_Frame.ply
    new file: Engineering/Software/PCL-Realsense-Capture/RS_Testing/RS-Frame_Capture.cpp
    [Captured_Frame.ply]
2018-06-15 Revert "Color data added to PLY format capture"
    This reverts commit 45eea62164c0b3fb86643c5e3cdbf70078805b96.
    modified: Engineering/Software/PCL-Realsense-Capture/RS_Testing/RS-Frame_Capture.cpp
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2018-06-23 Color stream coordinates stored in points format, needs testing
    [Captured_Frame.ply]
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2018-06-25 Lidar Motor Assembly v2
    2 piece enclosed box model that looks cooler
    [Lidar Assembly v2.f3d]
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2018-07-08 Schematic PDF fixed
2018-07-08 Inductor valued corrected
    [3D-ROMAP FINAL PSU.DSN]
2018-07-08 Final PSU complete
    Moving to production of board
    [3D-ROMAP FINAL PSU.DSN, Testboard-BOM.csv]
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2018-07-10 Schematic BOM added, and pages fixed
    [3D-ROMAP-PSU-BOM.csv, Digikey-BOM.csv]
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2018-07-17 PSU gerber fixed
    [3D-ROMAP-PSU.step]
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2018-07-18 Corrected drill holes and outline
    [3D-ROMAP-PSU.step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]
2018-07-19 Final board commit, fixed for layout
    [3D-ROMAP-PSU.step]
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2018-07-28 Old PCL fix
    [Captured_Frame.ply]
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2018-10-03 Chassis Component - Back
    Back face of the Chassis model to be cut.
    [Chassis Face Back.stl]
2018-10-03 Chassis Component - Front
    Front face of the Chassis model to be cut.
    [Chassis Face Front.stl]
2018-10-03 Chassis Component - Left
    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
    [Chassis Face Left.stl]
2018-10-03 Chassis Component - Right
    Right face of the Chassis model to be cut.
    [Chassis Face Right.stl]
2018-10-03 Chassis Component - Base
    Base face of the Chassis model to be cut.
    [Chassis Face Base.stl]
2018-10-03 Chassis Component - Bottom
    Bottom face of the Chassis model to be cut.
    [Chassis Face Bottom.stl]
2018-10-03 Chassis Component - Top
    Top face of the Chassis model to be cut.
    [Chassis Face Top.stl]
2018-10-03 OChassis - Battery Clip - Base
    Base face of the retired Chassis model to be cut.
    [Battery Clip Base.stl]
2018-10-03 OChassis - Battery Clip - 1
    Clip1 piece of the retired Chassis model to be cut.
    [Battery Clip1.stl]
2018-10-03 OChassis - Battery Clip - 2
    Clip2 piece of the retired Chassis model to be cut.
    [Battery Clip2.stl]
2018-10-03 OChassis - Battery Clip - 3
    Clip3 piece of the retired Chassis model to be cut.
    [Battery Clip3.stl]
2018-10-03 OChassis - Battery Clip - 4
    Clip4 piece of the retired Chassis model to be cut.
    [Battery Clip4.stl]
2018-10-03 OChassis - Battery Clip - 5
    Clip5 piece of the retired Chassis model to be cut.
    [Battery Clip5.stl]
2018-10-03 OChassis - Battery Clip - 6
    Clip6 piece of the retired Chassis model to be cut.
    [Battery Clip6.stl]
2018-10-03 OChassis - FatThinBase - Fat Base
    Fat Base face of retired Chassis model to be cut.
    [Fat Base.stl]
2018-10-03 OChassis - FatThinBase - Thin Base
    Thin Base face of retired Chassis model to be cut.
    [Thin Base.stl]
2018-10-03 OChassis - Lid1 - FatBase
    Fat Base (1) face of retired Chassis model to be cut.
    [Fat Base (1).stl]
2018-10-03 OChassis - Lid1 - ThinBase
    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
    [Thin Base (1).stl]
2018-10-03 OChassis - Lid1 - Vertical Support 1
    Vertical Support 1 piece of retired Chassis model.
    [Vertical Support1.stl]
2018-10-03 OChassis - Lid1 - Vertical Support 2
    Vertical Support 2 piece of retired Chassis model.
    [Vertical Support2.stl]
2018-10-03 OChassis - Lid1 - Vertical Support 3
    Vertical Support 3 piece of retired Chassis model.
    [Vertical Support3.stl]
2018-10-03 OChassis - Lid1 - Vertical Support 4
    Vertical Support 4 piece of retired Chassis model.
    [Vertical Support4.stl]
2018-10-03 Movement Motor Mount
    3D printed mount to attach motor to chassis
    [Movement Motor Mount.stl]
2018-10-03 Movement Motor Back Mount
    Support mount to stabilize the movement motor against the chassis.
    [Movement Motor Back Mount.stl]
2018-10-03 Physical Component - ARM
    3D model of Physical Component - ARM
    [ARM.stl]
2018-10-03 Physical Component - Battery1
    3D model of Physical Component - Battery1
    [Battery1.stl]
2018-10-03 Physical Component - Battery2
    3D model of Physical Component - Battery2
    [Battery2.stl]
2018-10-03 Physical Component - Jetson
    3D model of Physical Component - Jetson
    [Jetson.stl]
2018-10-03 Physical Component - MMount1
    3D model of Physical Component - MMount1
    [MMount1.stl]
2018-10-03 Physical Component - MMount2
    3D model of Physical Component - MMount2
    [MMount2.stl]
2018-10-03 Physical Component - Motor1
    3D model of Physical Component - Motor1
    [Motor1.stl]
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2018-10-03 Mechanical - Work Area
    Single environment where components can interact with each other.
    [Work Area.f3d]
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2018-11-28 Fixed error caused by fractions
    [main.c]
2018-11-28 PWM bug fixed
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2018-12-11 3D Printed Parts
    STL files of all needed 3D printed parts added to 3D Printed Parts folder
    [Battery Mount v2.stl, Caster Mount.stl, Face Clip Mount.stl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]
2018-12-11 3DROMAP_Chassis
    Files added for laser cut chassis. Schematic available in .AI .DXF and .SVG format.
    [3DROMAP_Chassis.dxf]
2018-12-11 3DROMAP_Chassis_Condensed
    Files added for laser cut chassis. Pieces condensed to smaller area with shorter laser travel time. Schematic available in .AI .DXF and .SVG format.
    [3DROMAP_Chassis_condensed.dxf]
2018-12-11 3DROMAP_Chassis_Top_with_Mounting_Holes
    Files added for laser cut chassis lid with mounting holes. Seperate piece if using Acrylic Top. Schematic available in .DXF and .SVG format.
    [3DROMAP_Chassis_Top_with_Mounting_Holes.dxf]
2018-12-11 Completed Assembly
    Completed Assembly file updated with final PNG of chassis model as well as .F3D file for future manipulation.
    [Work Area.f3d]
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2018-12-11 Physical Components
    Physical Components folder updated with STLs of all large compontents used in project.
    [ARM.stl, Jetson.stl, MMount1.stl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]
2018-12-11 Power Supply Assembly
    Power Supply Assembly folder updated with PDF and STEP files of power supply layout
    [3D-ROMAP-PSU.step]
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
